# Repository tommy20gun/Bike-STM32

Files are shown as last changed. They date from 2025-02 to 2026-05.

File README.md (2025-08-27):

# E-Bike Infotainment System

## Software Module Summary
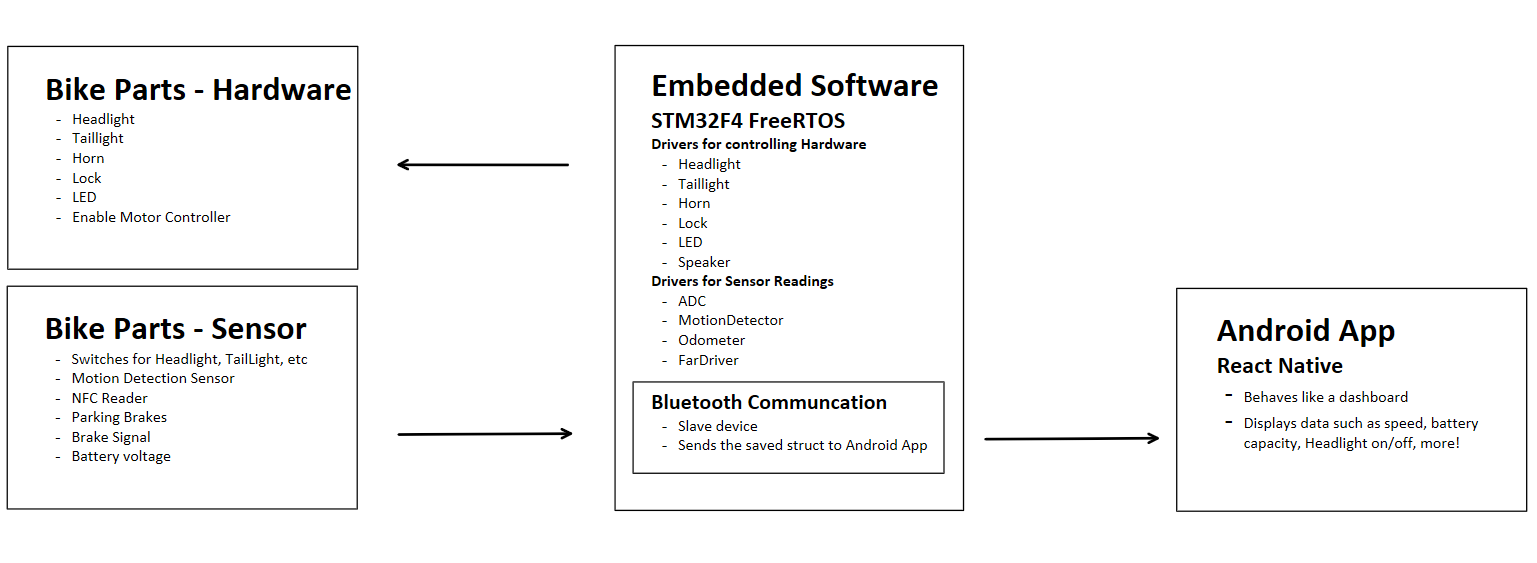
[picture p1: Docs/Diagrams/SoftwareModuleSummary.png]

The three modules are comprised of **Hardware, Embedded Software, and Android App Software.**
- The Microcontroller is an STM32F4 microcontroller running **FreeRTOS**. Each peripheral has a separate task that handles the firmware drivers for its operation. This allows certain peripherals that demand **ontime scheduling** to get their share of clock cycles.
- Embedded Software contains drivers for accessing:
  - **headlights, tail lights, car horn** - GPIO debounced switch, mosfet, relays
  - **NFC scanner and keycard unlock** - SPI communication with NFC chip (PN532)
  - **PWM LED lights** - PWM driver for WS2812B to control color
  - **Human detection alarm** - Interrupt driven by IR sensor
  - **Serial communication** - UART DMA to Bluetooth module
  - **Battery monitoring** - ADC, battery curve implemented as a polynomial regression
  - **Speedometer** - Hall effect sensor on wheel
- The Microcontroller sends **Bluetooth (BLE) data** to the Android Tablet.
- The display is an Android Tablet running a **mobile app** created using **React Native**

<a href="https://github.com/tommy20gun/Bike-STM32/tree/master/CustomDrivers"><strong>Explore the Code » </strong> </a>

<p align="right">(<a href="#readme-top">back to top</a>)</p>

## Demo

### Turn Signals
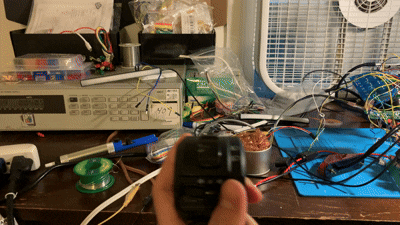
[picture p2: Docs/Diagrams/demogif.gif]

<p align="right">(<a href="#readme-top">back to top</a>)</p>

### Microcontroller Pinout -  KiCAD EDA:

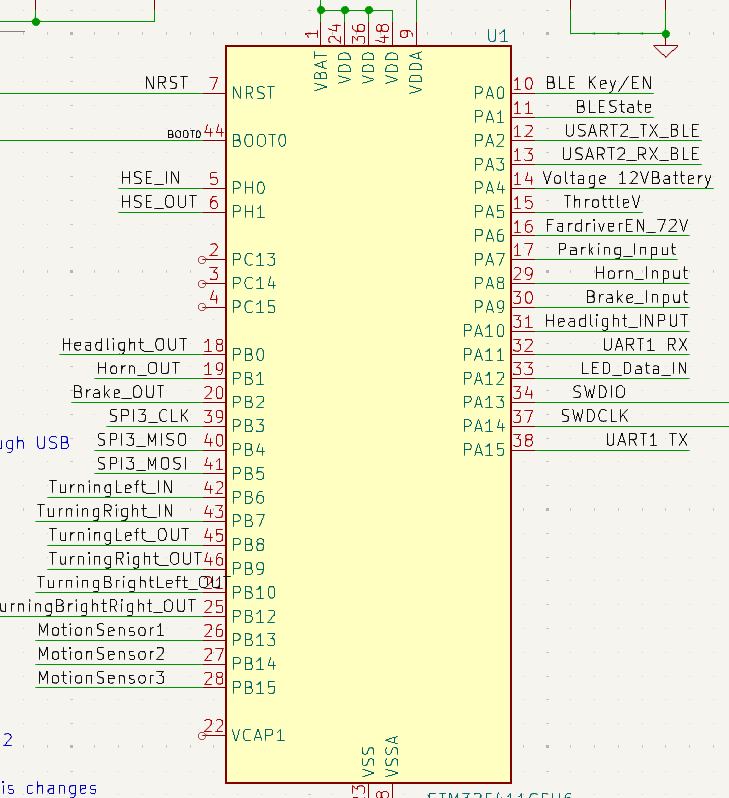
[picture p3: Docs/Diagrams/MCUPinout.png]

<a href="https://github.com/tommy20gun/Bike-STM32/tree/master/Docs/Diagrams/Bike_PCB.pdf"><strong>Explore the eCAD » </strong> </a>
<p align="right">(<a href="#readme-top">back to top</a>)</p>

### Battery Curve
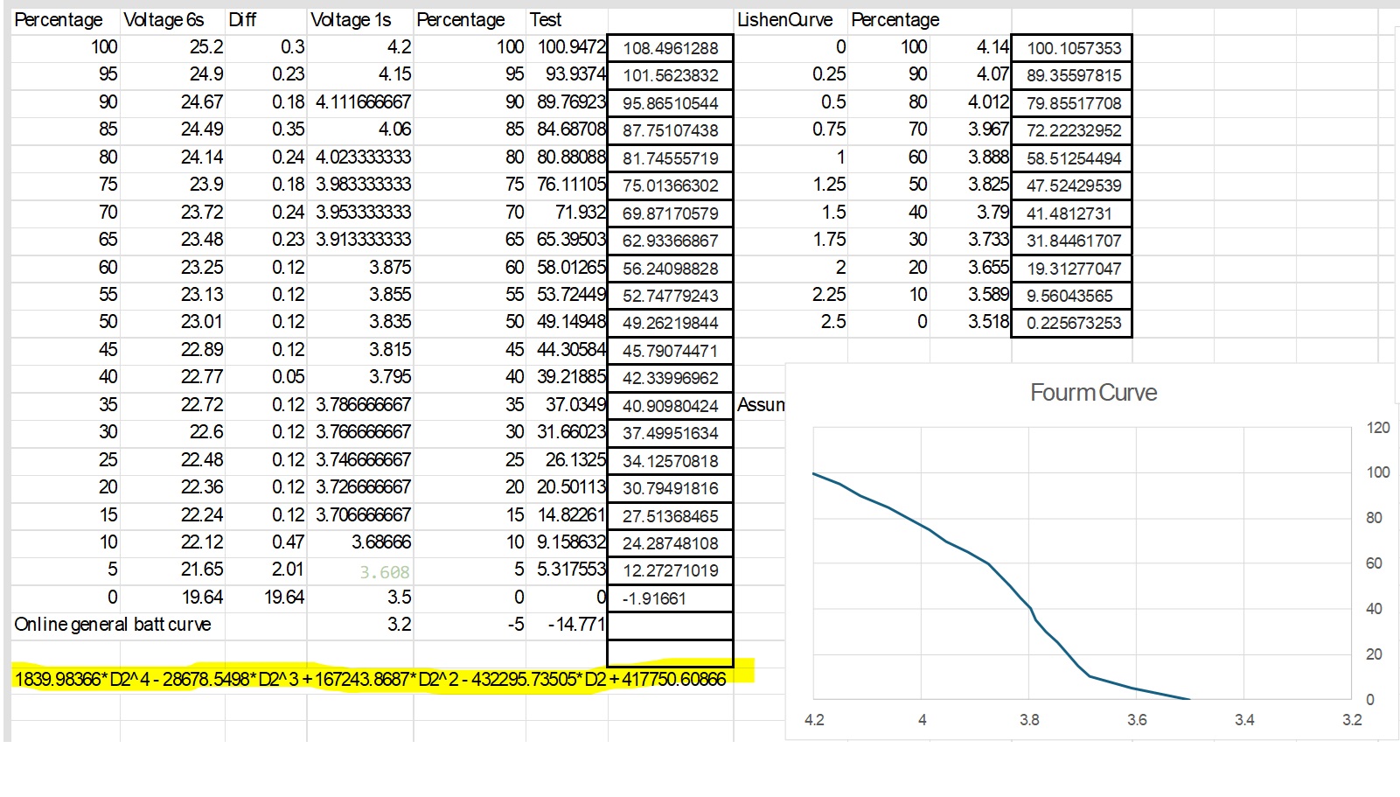
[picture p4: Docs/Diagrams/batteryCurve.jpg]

<p align="right">(<a href="#readme-top">back to top</a>)</p>

### State Machine Implementation of Lock

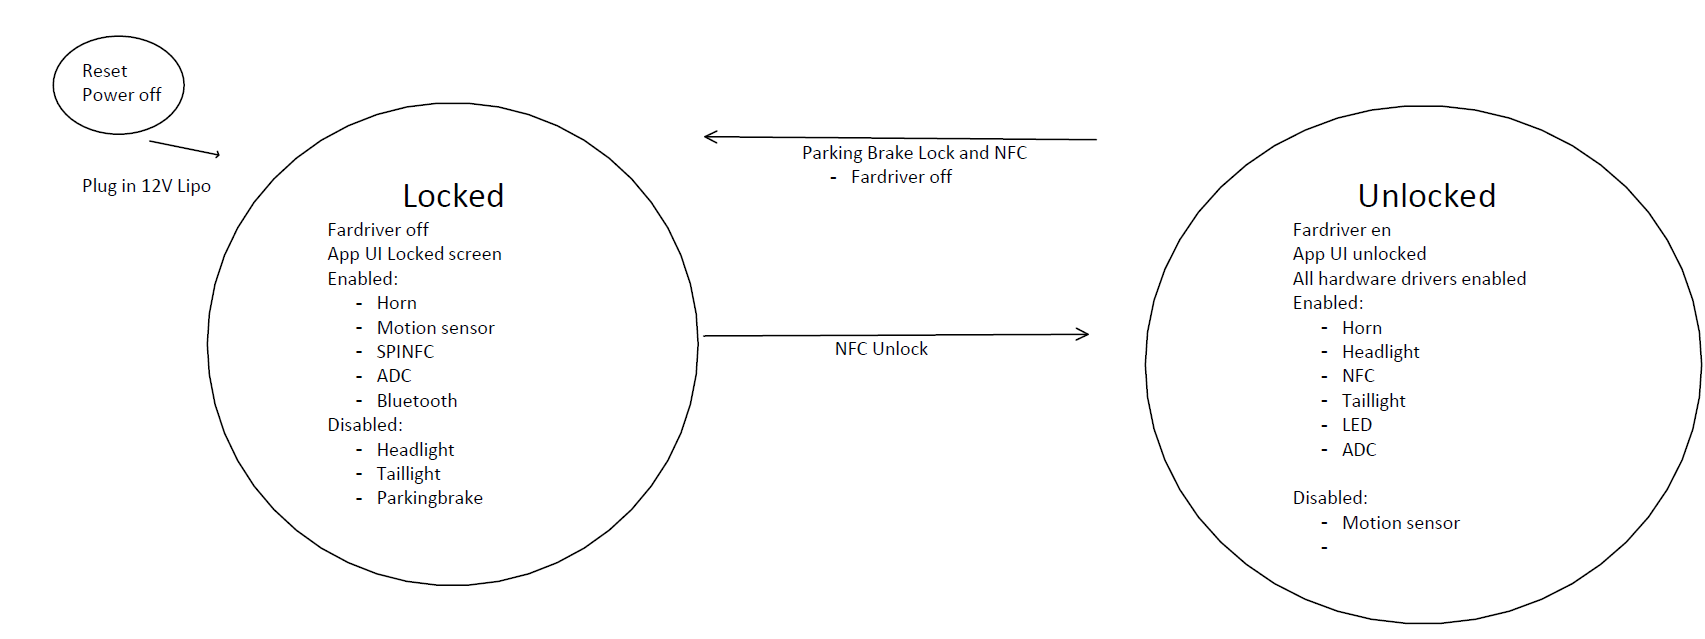
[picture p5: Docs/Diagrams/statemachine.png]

<p align="right">(<a href="#readme-top">back to top</a>)</p>

### Bike
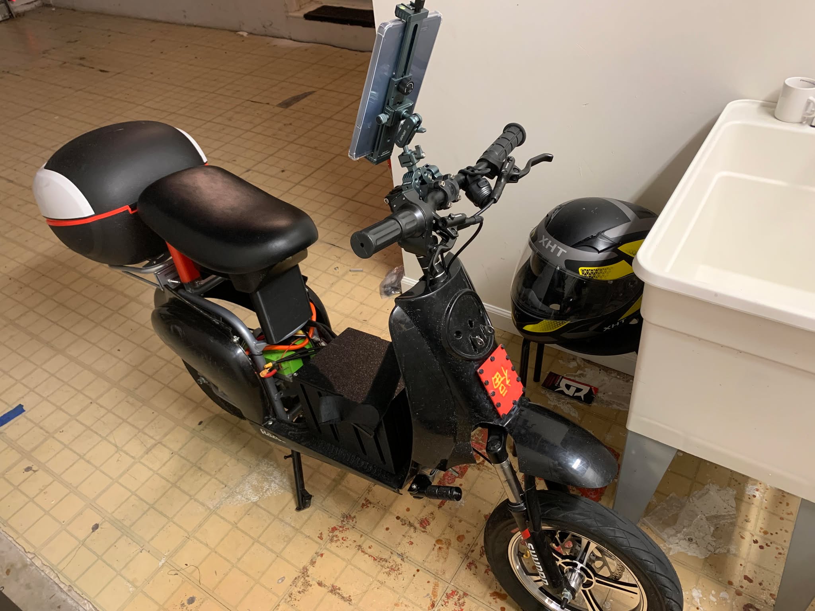
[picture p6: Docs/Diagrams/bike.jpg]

<!-- LICENSE -->
## License

Distributed under the MIT License. See `LICENSE-MIT.txt` for more information.

<p align="right">(<a href="#readme-top">back to top</a>)</p>

<!-- CONTACT -->
## Contact

Tommy Xu: xuhaohui20@gmail.com

<p align="right">(<a href="#readme-top">back to top</a>)</p>

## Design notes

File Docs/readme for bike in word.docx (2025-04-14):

# Smart E-Bike Project

This repository contains the implementation of a Tesla Center Console-like system mounted on an electric motorcycle.

- The display is an Android Tablet running a mobile app created using React Native
- Hardware I am controlling includes headlights, tail lights, car horn, NFC scanner and keycard unlock, cool LED lights, human detection alarm, and more!
- The Central Computer is an STM32F4 microcontroller running FreeRTOS. It allows all hardware to be controlled via the control cluster of the handlebar of the bike.
- The Central Computer sends Bluetooth data to the Android Tablet.

Below is a picture of the bike:

Below is a detailed diagram of each component and its features and functions:

Below is the state machine implementation of the Locking and Unlocking of the bike:

Below is the Microcontroller Pinout made with KiCAD EDA:

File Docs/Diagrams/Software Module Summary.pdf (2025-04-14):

# Headlight.h

- Setup GPIO EXTI,GPIO OD
- Toggle output on EXTI
•

# TailLight.h

Setup GPIO EXTI,GPIO OD,
Timer, GPIO PP

•

EXTI triggered inputs:
- Brake
- Left blink
- Right blink

•

- Blinks respective light at 1hz GPIO PP Hardware signal to FarDriver

•

Triggers a bluetooth command to blink on UI.

•

TODO: Should I poll the
variable and just call it a day?

•

# Drivers for controlling Hardware

Class Constructor runs the setup and creates RTOS task. Instance of object lives in mai

# Horn.h

- Setup GPIO EXTI,GPIO OD
- Toggle output on EXTI
•

# LED.h

- Setup DMA, GPIO PWM
Lights should move down its strand relative to the speed of the bike

•

Translate speed/ throttle
voltage of bike to speed of LED motion

•

Send data to light IC through DMA and PWN

•

## LEDMessage.h

Prepare the 32bit
message

•

Abstract color and
brightness

•

# Lock.h

- Setup SPI, GPIO PP, State Locked
- SPI CS En
- NFC Hardcoded Password
- SPI read toggles lock state Parking_Input pin moves state Unlocked -> locked. Does not unlock the bike

•

- Parking_Input disables Fardriver Sends BLE commands for locked and unlocked state

•

Triggers alarm upon use of buttons in locked state

•

TODO later: implement low
power mode into this

# MotionDetector

- Setup GPIO Input
- Activate on Lock state
- Deactivate on Unlock state Implement detection threshold algorithm

•

Enable Speaker/Horn on
detection

•

# Speaker.h

# ADC.h

12V battery. 3:1 voltage divider with outside resistor going into analog pin.

•

- Throttle V

# Bluetooth.h - BLE Slave device

### BluetoothSendslow()

Bluetooth TX Pollling 5hz using DMA since the data struct will be stationary

BluetoothSendFast()
Bluetooth TX Polling 50hzusing DMA since the data struct will be stationary

### BluetoothSendSpecialCom mand()

Upon request notify the
master(phone) of a change in state

BMSMOSon() should be a
command sent to ANTBMS

# React Native App - Android

Display
- Speedometer
- Odometer
- Wattage/Current
- RPM/ThrottleV
- Battery percentage: 12V, 72V optional
- TurnSIgnal Blink
- MotorTemp
- HeadlightON
- Brake On
- HornON is a red screen LOL
- Bool* BMSMOSOn (optional) sent to antBMS as a command 'A5A5FA0000FA' # Turn Off Charge MOSFET 'A5A5FA0001FB' # Turn On Charge MOSFET 'A5A5FE0000FE' # Reboot BMS
'A5A5F90000F9' # Turn Off DisCharge MOSFET 'A5A5F90001FA' # Turn On DisCharge MOSFET
'A5A5FC0000FC' # Toggles balancing

From <https://diysolarforum.com/threads/for-those-of-you-looking-to-monitor-your-ant-bms-with-pi3-via-bluetooth.6726/page-5> (https://diysolarforum.com/threads/for-those-of-you-looking-to-monitor-your-ant-bms-with-pi3-via-bluetooth.6726/page-5)

# Fardriver

# ANT BMS BT2.0

## Data sent

ANT BMS
This is bluetooth 2.0
0xDBDB00000000 to Receive 140 bytes of data
Python code: For those of you looking to monitor your ANT-BMS with
Pi3 via Bluetooth. | Page 4 | DIY Solar Power Forum (https://diysolarforum.com/threads/for-those-of-you-looking-to-monitor-your-ant-bms-with-pi3-via-bluetooth.6726/page-4)
- Current
- Pack Voltage
- unitVDiff
- All Cell Unit V (optional)
- Battery Temperature (optional)

# - 12V Lipo - Throttle potentiometer

# Buttons and Sensors

- HeadlightON/ HeadlightOFF
- Turn Signal Left/Right/OFF
- HornON
- ParkingON
- Boost (optional)
- 3 motion detection sensor
- NFC Reader

# Hardware

# Embedded Software - STM32F4

- Headlights
- Tailight
- Horn
- LED
- Speakers
- Brake
- FardriverEnable 72V

# Bike Parts - Output

# Bike Parts - Input

Commands to send to Controller (once low power mode is enabled)
- Turn on Horn
- Turn on Light
- Turn on LED

# Odometer.h

- EEPROM emulation on variable Calculates Odometer reading based on dspeed/dtime

•

Optional
- Set up GPIO Exti
- Trigger every Hall Effect contact Update odometer per increment of wheel rotation

•

### Setup using AT Commands

- Configured as slave
Pair bind link to the phone to allow for connection in range (done on master device)

- Name:deez nuts
- PW: 6969
- Baud:9600
- Stop:1
- Parity 0

TODO: switch on circuit board to allow for programming in AT mode

TODO Turn the EN pin to input to read the switch whether want AT mode or regular

- Uint32_t magic number = 69420
- Bool* HeadlightON
- Double* MotorTemp
- Double* ADCreading72V
- Double* ADCreading12V
- Double* Battery temp
- Struct* PackVoltage(optional)
- Double* Odometer (Persistent)

# Bluetoth Communication HashTable

- Currently lives in bluetooth.h
- There won't be race conditions using a freeRTOS queue. 1 source of writing This will change when Android commands are introduced, the UART channel needs mutex before

- Error check with CRC
Use a Queue to send data to the packing struct, once the queue is empty then data can be sent.

- Priority for sending is lower than hardware buttons
- Double* speed
- Bool* HornON
- Bool* BrakeON
- Bool* TurningLeft
- Bool* TurningRight
- Int* RPM
- Double* Current
- Double* throttleV
- State_t* locked
- State_t* unlocked
- uint32_t CRC

# FarDriver.h

- RPM
- Motor Temperature

Wiring method

GPIO input with timer on 5v tolerant pins

•

ADC read the temperature
sensor

•

Bluetooth method
Baud:19200. data format is noted here. Just try to receive it using HC-05 serial
fardriver-controllers/README.md at main · jackhumbert/fardriver-controllers (https://github.com/jackhumbert/fardriver-controllers/blob/main/README.md)

# Drivers for sensor readings

Attempt with BLE bc there is a chance ANT BMS is BLE

# Watchdog timer

# Software Module Summary

Tuesday, February 4, 2025 9:51 PM

New Section 2 Page 1

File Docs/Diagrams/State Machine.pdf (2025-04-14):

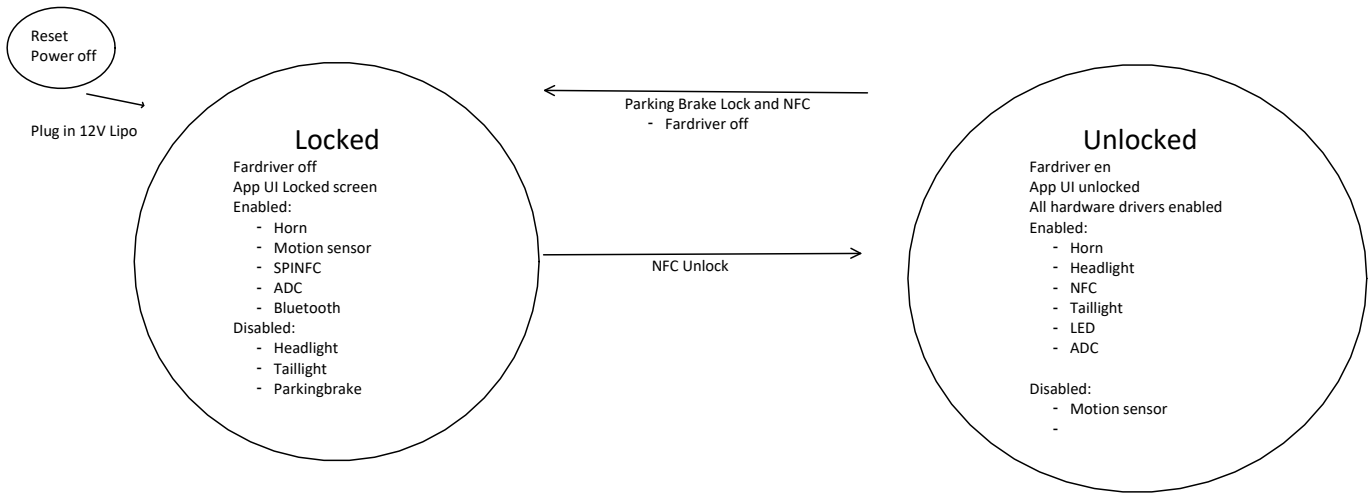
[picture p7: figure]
NFC Unlock; Parking Brake Lock and NFC - Fardriver off Locked; Fardriver off App UI Locked screen Enabled: - Horn - Motion sensor - SPINFC - ADC - Bluetooth Disabled: - Headlight - Taillight - Parkingbrake; Unlocked; Fardriver en App UI unlocked All hardware drivers enabled Enabled: - Horn - Headlight - NFC - Taillight - LED - ADC; Disabled: - Motion sensor -; Reset Power off; Plug in 12V Lipo

Main ()
RTOS task state machine:
- state transition lock to unlock
- State transition unlocked to lock

vtasksuspend() and vtaskresume() is implemented depending on the transition Or use a class specific state transition function

Lock.cpp (only the drivers to send an event)
Read lock and send the event to the state transition task

# State Machine

Wednesday, February 5, 2025 4:59 PM

New Section 2 Page 1

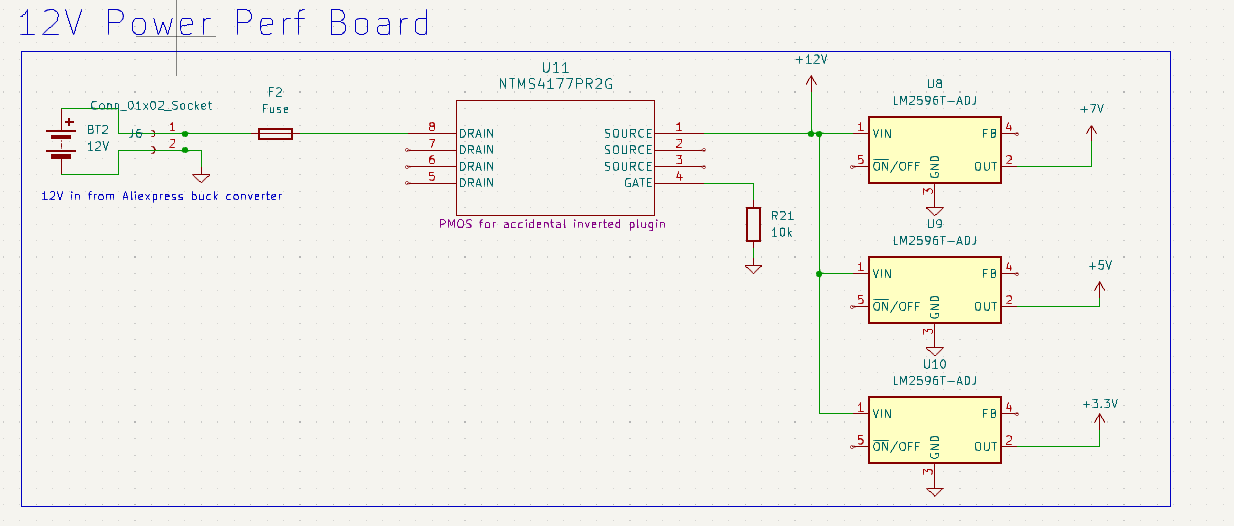
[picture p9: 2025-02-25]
Docs/Diagrams/KiCAD Power.png

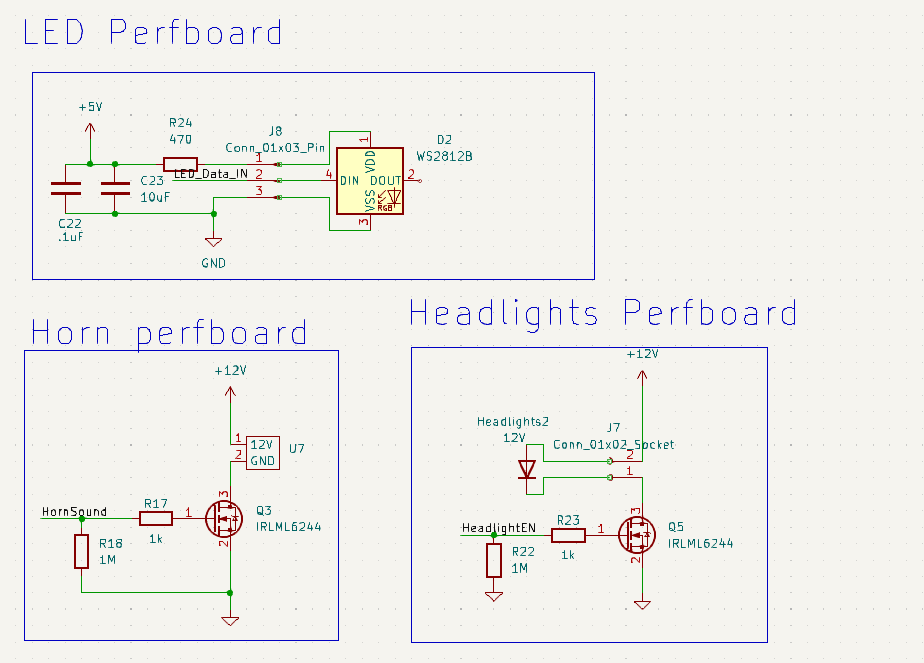
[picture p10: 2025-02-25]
Docs/Diagrams/KiCAD etc.png

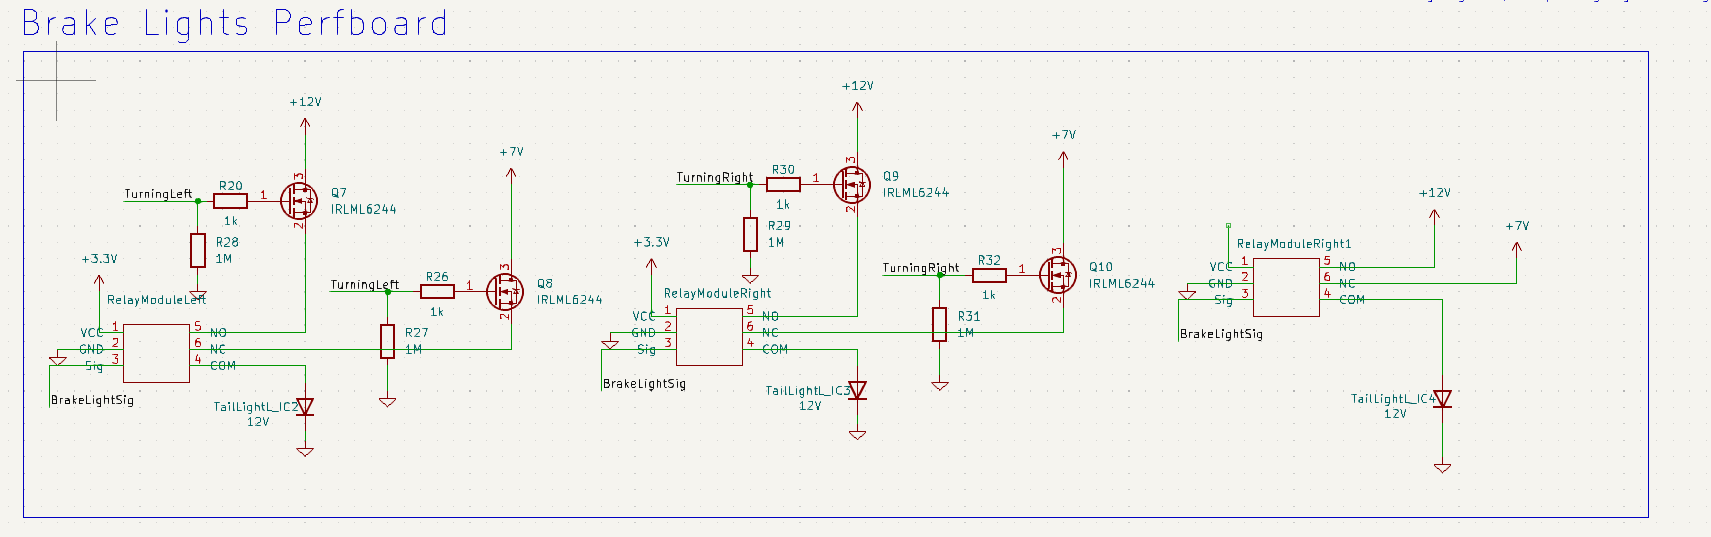
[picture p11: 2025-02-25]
Docs/Diagrams/KiCAD brake lights.png

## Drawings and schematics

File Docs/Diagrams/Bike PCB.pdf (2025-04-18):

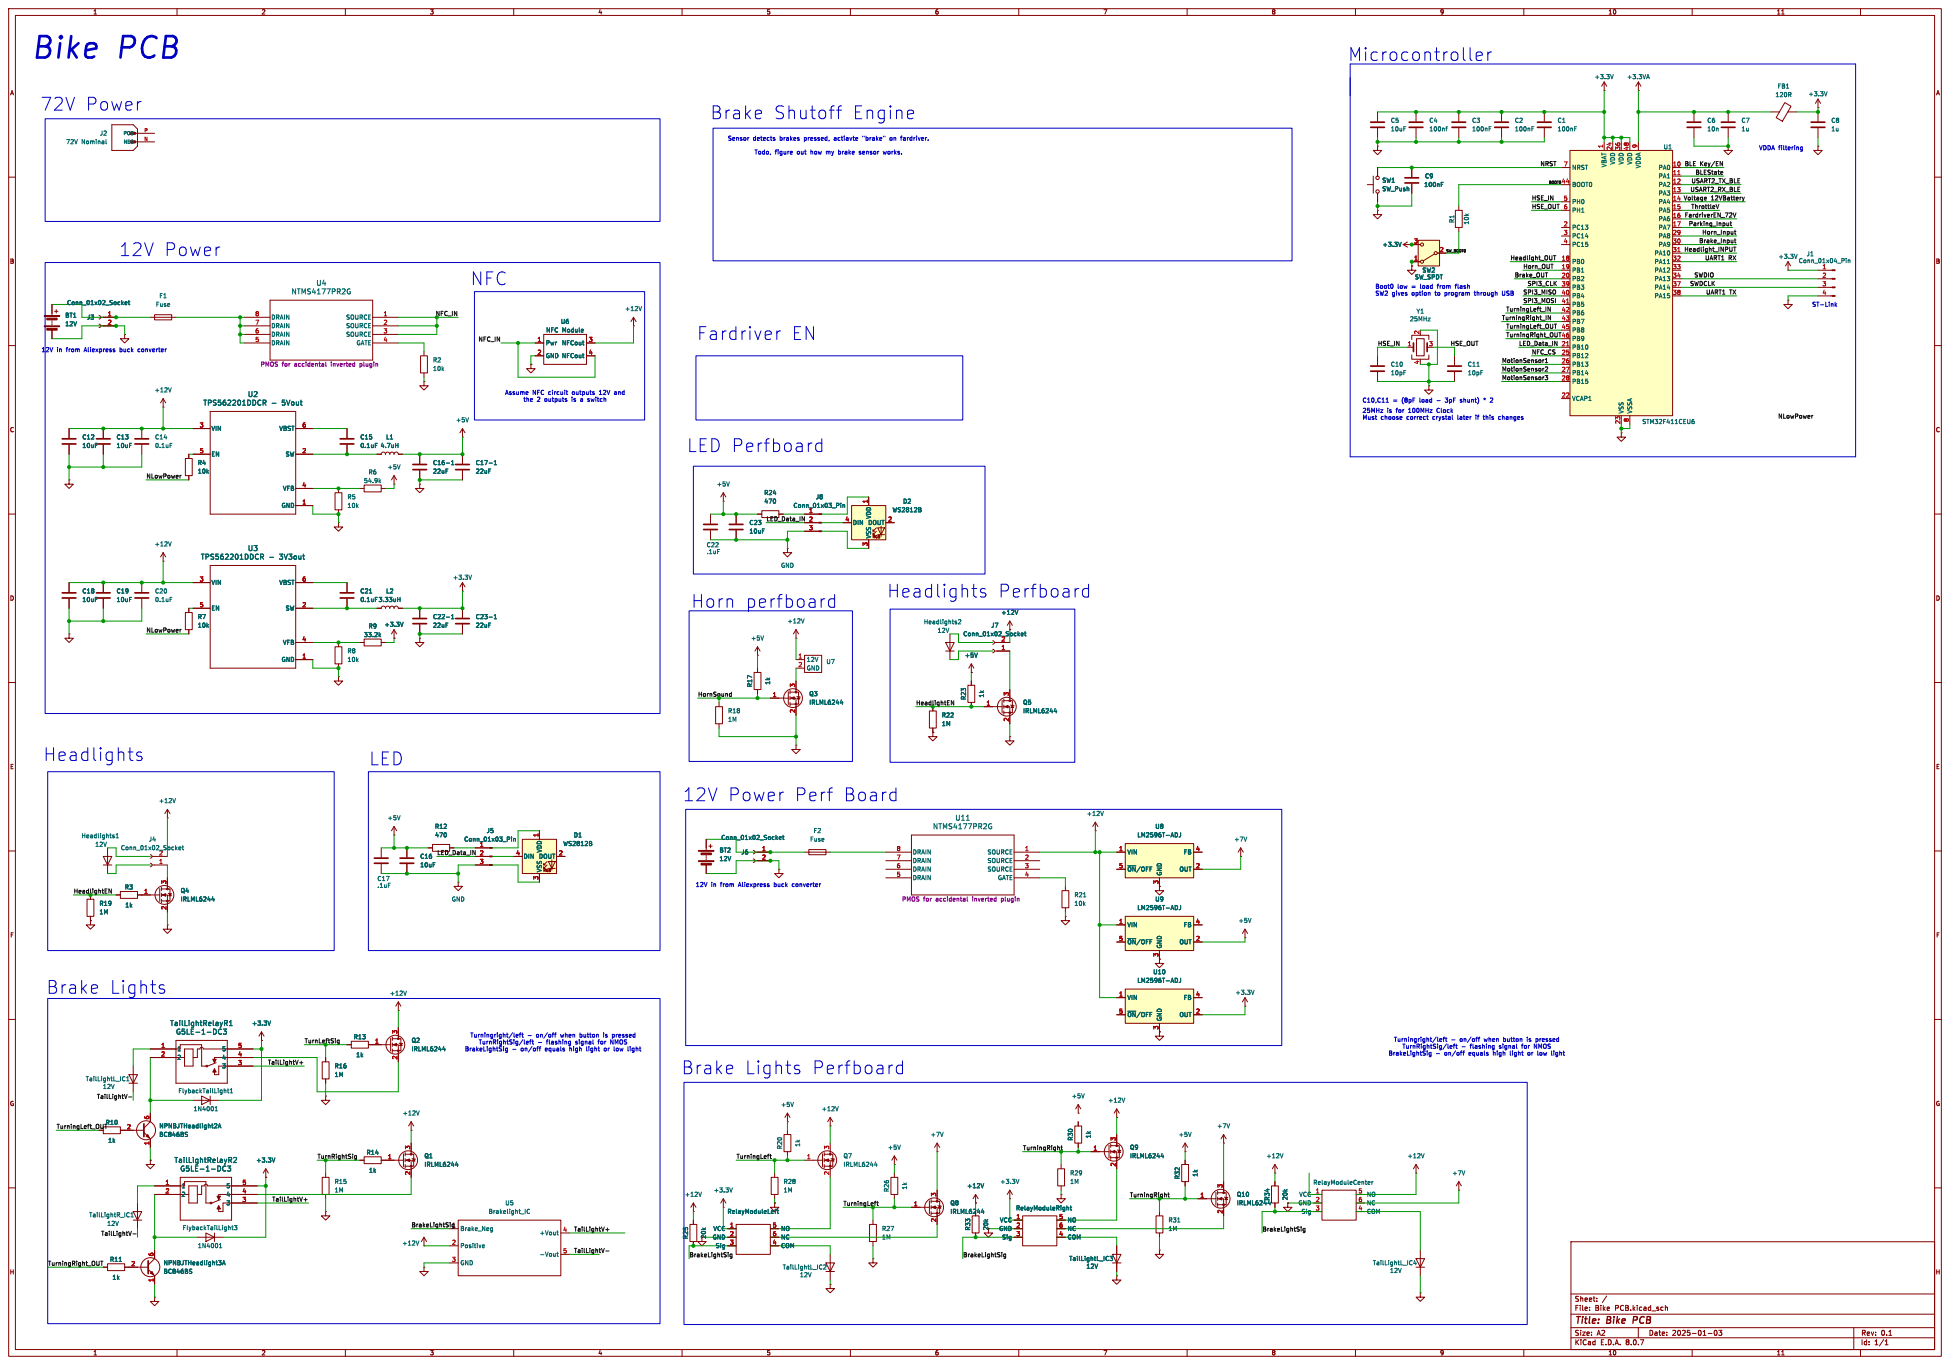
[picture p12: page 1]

ST-Link C10,C11 = (8pF load - 3pF shunt) * 2

25MHz is for 100MHz Clock Must choose correct crystal later if this changes (https://www.digikey.com/en/products/detail/ecs-inc/ECS-250-9-37B2-CKM-TR/14663267)

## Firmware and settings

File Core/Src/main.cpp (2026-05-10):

 /** 
  * 
  * @brief          : Main program body
  * 
  * This is the main body of the program. The MCU will run setup code such as Clock config, ISRVector table, and start the RTOS.
  * Implements state machine.
  *
  * 
  */

#include "main.h" //includes LL
#include <string>

#include "Peripheral_initialization.h"

//CPP includes
#include "Headlight.h"
#include "Horn.h"
#include "Bluetooth.h"
#include "MemoryMap.h"
#include "Speedometer.h"
#include "Motion_Detector.h"
#include "LED.h"
#include "Lock.h"
#include "Taillight.h"
#include "ADC.h"
#include "SwitchActivatedDevice.h"


static Horn* horn;
static ShortHorn* shorthorn;
static Headlight* headlight;
static TailLight_Turn* left;
static TailLight_Turn* right;
static TailLight_Brake* brake;
static Bluetooth* bluetooth;
static ADCDriver* adc;
static Lock* bikelock;
static Motion_Detector* detector1;
static Speedometer* speedometer;
//static Motion_Detector* detector2;
//static Motion_Detector* detector3;

static TaskHandle_t stateMachineHandle;
static state_t state;
static QueueHandle_t messenger;

/* create tasks, create object instances. object constructors set up hardware and own the semaphore*/
void GlobalSetup(void){
    //create global queue, assign to all obj
  messenger = xQueueCreate(30,sizeof(struct uint32_t_Buffer));
  BaseType_t xReturned = xTaskCreate(state_machine, "state_machine", 64, NULL, 2, &stateMachineHandle);
  if (xReturned != pdPASS){
    Error_Handler();
  }

  horn = new Horn(GPIOA,GPIO_PIN_8,GPIOB,GPIO_PIN_1,messenger,HORN_ON);
  shorthorn = new ShortHorn(GPIOB,GPIO_PIN_14, GPIOB,GPIO_PIN_1,messenger,HORN_ON);
  headlight = new Headlight(GPIOA,GPIO_PIN_10,GPIOB,GPIO_PIN_0,messenger,HEADLIGHT_ON);
  left = new TailLight_Turn(GPIOB,GPIO_PIN_6,GPIOB,GPIO_PIN_8,GPIOB,GPIO_PIN_10,messenger,TURNING_LEFT);
  right = new TailLight_Turn(GPIOB,GPIO_PIN_7,GPIOB,GPIO_PIN_9,GPIOB, GPIO_PIN_12,messenger,TURNING_RIGHT);
  brake = new TailLight_Brake(GPIOA,GPIO_PIN_9,GPIOA,GPIO_PIN_5,messenger,BRAKE_ON);
  bluetooth = new Bluetooth(messenger); //bluetooth hard coded to PA2,PA3
  adc = new ADCDriver(messenger, GPIOA, GPIO_PIN_4, GPIO_PIN_0); //VOLTAGE_12V_BATT and PERCENT_12V_BATT are hardcoded. channel4 (12V) PA4 is hardcoded. So is Queuetag
  bikelock = new Lock(GPIOA,GPIO_PIN_7,GPIOA,GPIO_PIN_6,messenger,STATE_MACHINE_STATUS,stateMachineHandle);
  speedometer = new Speedometer(messenger, GPIOA, GPIO_PIN_1);
  //detector1 = new Motion_Detector(messenger,HEADLIGHT_ON, GPIOB, GPIO_PIN_13);
  xTaskNotify(stateMachineHandle, 2, eSetValueWithOverwrite); //increments notif value by 1. TODO this is wrong bc then state 1 is unlock but I should check notified value to confirm.
}

//TODO there is a possiblity to implement lock level 2 for motion detection
/*
State machine should stay in main
*/
void state_machine(void* pvParameters){
  state = STATE_START;
  typedef state_t (*state_Transition)(state_t);
  state_Transition transitiontable[3] = {lock,unlock, start};
  uint32_t notifiedValue = 0;
  while(1){
    xTaskNotifyWait(0, 2U, &notifiedValue, portMAX_DELAY); //Start is not block bc of this  xTaskNotify(stateMachineHandle, 2, eSetValueWithOverwrite); //increments notif value by 1. TODO this is wrong bc then state 1 is unlock but I should check notified value to confirm.

    //notified value is the same enumeration where 1 calls unlock 0 calls locked
    //STATE_UNLOCKED = 1
    //STATE_LOCKED = 0
    if (state == STATE_START){
      state = transitiontable[notifiedValue & 3U](state); //reads the last bit to determine 0 or 1
    }
    else {
      state = transitiontable[notifiedValue & 1U](state); //reads the last bit to determine 0 or 1
    }
  }
}
//TODO future make this an event group where the notification uint32 has mapping of each task handle
/*
FardriverEN_72V - PA6
*/
state_t unlock(state_t state){
  if (state == STATE_LOCKED){
    vTaskResume(horn->getTaskHandle());
    vTaskResume(left->getTaskHandle());
    vTaskResume(right->getTaskHandle());
    vTaskResume(brake->getTaskHandle());
    LL_GPIO_ResetOutputPin(GPIOA,GPIO_PIN_6); //fardriver Pin
    //vTaskResume(LED);
    //vTaskSuspend(detector1->getTaskHandle());
    honkHorn(state);
    //log stateUnlocked suscessful
    return STATE_UNLOCKED;
  }
  //log stateunlocked failed
  return STATE_LOCKED;
}
/*
FardriverEN_72V - PA6
*/
state_t lock(state_t state){
  if (state == STATE_UNLOCKED){
    vTaskSuspend(horn->getTaskHandle());
    vTaskSuspend(left->getTaskHandle());
    vTaskSuspend(right->getTaskHandle());
    vTaskSuspend(brake->getTaskHandle());
    LL_GPIO_SetOutputPin(GPIOA,GPIO_PIN_6); //fardriver Pin will close OD, close relay, locking the bike 
    //vTaskSuspend(LED);
    //vTaskResume(detector1->getTaskHandle());
    honkHorn(state);
    //log stateUnlocked suscessful
    return STATE_LOCKED;
  }
  //log stateunlocked failed
  return STATE_UNLOCKED;
}

state_t start(state_t state){
  if (state == STATE_START){
    LL_GPIO_SetOutputPin(GPIOA,GPIO_PIN_6); //fardriver Pin will close OD, close relay, locking the bike 
    vTaskSuspend(horn->getTaskHandle());
    vTaskSuspend(left->getTaskHandle());
    vTaskSuspend(right->getTaskHandle());
    vTaskSuspend(brake->getTaskHandle());
    //vTaskSuspend(LED);
    vTaskResume(detector1->getTaskHandle());
    //log stateUnlocked suscessful
    return STATE_LOCKED;
  }
  //log stateunlocked failed
  return state;
}

void honkHorn(state_t func_call_state){
  if (func_call_state == STATE_UNLOCKED || func_call_state == STATE_START){ //lock is 1 beep
    LL_GPIO_SetOutputPin(GPIOB, LL_GPIO_PIN_1);
    vTaskDelay(10);
    LL_GPIO_ResetOutputPin(GPIOB, LL_GPIO_PIN_1);
  }
  else {//unlock is 2 beep
    LL_GPIO_SetOutputPin(GPIOB, LL_GPIO_PIN_1);
    vTaskDelay(10);
    LL_GPIO_ResetOutputPin(GPIOB, LL_GPIO_PIN_1);
    vTaskDelay(100);
    LL_GPIO_SetOutputPin(GPIOB, LL_GPIO_PIN_1);
    vTaskDelay(10);
    LL_GPIO_ResetOutputPin(GPIOB, LL_GPIO_PIN_1);
  }
}

int main(){
  //HAL_Init(); //TODO Try to run code without this
  SystemClock_Config();
  GPIO_GlobalSetup();
  GlobalSetup();
  vTaskStartScheduler();
}

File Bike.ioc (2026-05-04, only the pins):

Mcu.UserName=STM32F411CEUx
PA1.Signal=ADCx_IN1
PA10.Signal=GPXTI10
PA11.Signal=GPXTI11
PA12.Signal=GPXTI12
PA13.Signal=SYS_JTMS-SWDIO
PA14.Signal=SYS_JTCK-SWCLK
PA2.Signal=USART2_TX
PA3.Signal=USART2_RX
PA4.Signal=ADCx_IN4
PA5.Signal=ADCx_IN5
PA7.Signal=GPXTI7
PB12.Signal=GPIO_Input
PB13.Signal=GPIO_Input
PB14.Signal=GPIO_Input
PB3.Signal=SPI3_SCK
PB4.Signal=SPI3_MISO
PB5.Signal=SPI3_MOSI
PB8.Signal=GPIO_Output
PB9.Signal=GPIO_Output
PC13-ANTI_TAMP.Signal=GPIO_Output

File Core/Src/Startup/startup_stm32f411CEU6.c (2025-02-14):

 /** 
  * 
  * @brief          : Set up vector table and reset entry point
  * 
  * Performs Reset Handler by allocating memory addresses and running main.
  * Creates ISRVector table.
  * 
  * Translation of startup_stm32f411xe.s which is in ARM Assembly. 
  * 
  */

#include <stdint.h>
#include <system_stm32f4xx.h>
#include <stm32f4xx.h>

/* address from Linker */
/*flash*/
extern uint32_t  _sidata; //start of data in flash
/* ram */
extern uint32_t _sdata; //start of data in ram
extern uint32_t _edata; //end of data in ram
extern uint32_t _sbss; //start of data in bss
extern uint32_t _ebss; //end of data in bss
extern uint32_t _estack; //stack pointer

//find all c++ objects and "execute" constructors
extern void __libc_init_array();
extern int main();

//main entry point to the program
void Reset_Handler(void){
	
    uint32_t* sidata = &_sidata;
    uint32_t* sdata = &_sdata;
    uint32_t* edata = &_edata;
    //move from flash into static ram
    while(sdata < edata){
        *sdata = *sidata;
		sdata++;
		sidata++;
    } 
    
	uint32_t* sbss = &_sbss;
	uint32_t* ebss = &_ebss;
    //initialize bss as 0
	while(sbss < ebss){
		*sbss = 0;
		sbss++;
	}
	
    SystemInit();
	//find all c++ objects and "execute" constructors
    __libc_init_array();
    main();

    /* code needs to execute if main somehow returns by accident*/
    while(1);

}
//unimplemented interrupts
void DefaultHandler(void){
	while(1);
}



//initialize all interrupt functions but give them the weak attribute so that it will use defaultHandler unless the function is implemented
__weak void   NMI_Handler(void){ DefaultHandler();}
__weak void   HardFault_Handler(void){DefaultHandler();}
__weak void   MemManage_Handler(void){ DefaultHandler();}
__weak void   BusFault_Handler(void){ DefaultHandler();}
__weak void   UsageFault_Handler(void){ DefaultHandler();}
__weak void   SVC_Handler(void){ DefaultHandler();}
__weak void   DebugMon_Handler(void){ DefaultHandler();}
__weak void   PendSV_Handler(void){ DefaultHandler();}
__weak void   SysTick_Handler(void){ DefaultHandler();}

/* External Interrupts */
__weak void      WWDG_IRQHandler                   (void){ DefaultHandler();}/* Window WatchDog              */                                        
__weak void      PVD_IRQHandler                    (void){ DefaultHandler();}/* PVD through EXTI Line detection */                        
__weak void      TAMP_STAMP_IRQHandler             (void){ DefaultHandler();}/* Tamper and TimeStamps through the EXTI line */            
__weak void      RTC_WKUP_IRQHandler               (void){ DefaultHandler();}/* RTC Wakeup through the EXTI line */                      
__weak void      FLASH_IRQHandler                  (void){ DefaultHandler();}/* FLASH                        */                                          
__weak void      RCC_IRQHandler                    (void){ DefaultHandler();}/* RCC                          */                                            
__weak void      EXTI0_IRQHandler                  (void){ DefaultHandler();}/* EXTI Line0                   */                        
__weak void      EXTI1_IRQHandler                  (void){ DefaultHandler();}/* EXTI Line1                   */                          
__weak void      EXTI2_IRQHandler                  (void){ DefaultHandler();}/* EXTI Line2                   */                          
__weak void      EXTI3_IRQHandler                  (void){ DefaultHandler();}/* EXTI Line3                   */                          
__weak void      EXTI4_IRQHandler                  (void){ DefaultHandler();}/* EXTI Line4                   */                          
__weak void      DMA1_Stream0_IRQHandler           (void){ DefaultHandler();}/* DMA1 Stream 0                */                  
__weak void      DMA1_Stream1_IRQHandler           (void){ DefaultHandler();}/* DMA1 Stream 1                */                   
__weak void      DMA1_Stream2_IRQHandler           (void){ DefaultHandler();}/* DMA1 Stream 2                */                   
__weak void      DMA1_Stream3_IRQHandler           (void){ DefaultHandler();}/* DMA1 Stream 3                */                   
__weak void      DMA1_Stream4_IRQHandler           (void){ DefaultHandler();}/* DMA1 Stream 4                */                   
__weak void      DMA1_Stream5_IRQHandler           (void){ DefaultHandler();}/* DMA1 Stream 5                */                   
__weak void      DMA1_Stream6_IRQHandler           (void){ DefaultHandler();}/* DMA1 Stream 6                */                   
__weak void      ADC_IRQHandler                    (void){ DefaultHandler();}/* ADC1, ADC2 and ADC3s         */                                 
__weak void      EXTI9_5_IRQHandler                (void){ DefaultHandler();}/* External Line[9:5]s          */                          
__weak void      TIM1_BRK_TIM9_IRQHandler          (void){ DefaultHandler();}/* TIM1 Break and TIM9          */         
__weak void      TIM1_UP_TIM10_IRQHandler          (void){ DefaultHandler();}/* TIM1 Update and TIM10        */         
__weak void      TIM1_TRG_COM_TIM11_IRQHandler     (void){ DefaultHandler();}/* TIM1 Trigger and Commutation and TIM11 */
__weak void      TIM1_CC_IRQHandler                (void){ DefaultHandler();}/* TIM1 Capture Compare         */                          
__weak void      TIM2_IRQHandler                   (void){ DefaultHandler();}/* TIM2                         */                   
__weak void      TIM3_IRQHandler                   (void){ DefaultHandler();}/* TIM3                         */                   
__weak void      TIM4_IRQHandler                   (void){ DefaultHandler();}/* TIM4                         */                   
__weak void      I2C1_EV_IRQHandler                (void){ DefaultHandler();}/* I2C1 Event                   */                          
__weak void      I2C1_ER_IRQHandler                (void){ DefaultHandler();}/* I2C1 Error                   */                          
__weak void      I2C2_EV_IRQHandler                (void){ DefaultHandler();}/* I2C2 Event                   */                          
__weak void      I2C2_ER_IRQHandler                (void){ DefaultHandler();}/* I2C2 Error                   */                            
__weak void      SPI1_IRQHandler                   (void){ DefaultHandler();}/* SPI1                         */                   
__weak void      SPI2_IRQHandler                   (void){ DefaultHandler();}/* SPI2                         */                   
__weak void      USART1_IRQHandler                 (void){ DefaultHandler();}/* USART1                       */                   
__weak void      USART2_IRQHandler                 (void){ DefaultHandler();}/* USART2                       */                   
__weak void      EXTI15_10_IRQHandler              (void){ DefaultHandler();}/* External Line[15:10]s        */
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

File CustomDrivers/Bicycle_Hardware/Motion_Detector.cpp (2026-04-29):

 /** 
  * 
  * @brief          : Driver to control Motion Detector
  * 
  * Driver to control Motion Detector circuit. 
  * Implementation of the detection threshold algorithm
  * 
  * GPIO EXTI 1- PB13
  * GPIO EXTI 2- PB14
  * GPIO EXTI 3- PB15
  * 
  * account for standby phase of 1 minute on startup
  * Pin going low is "detected motion"
  * there is a delay of 3 seconds (blocked after the pin going back HIGH)
  * THere is an adjustable time delay during the last time motion is detected BEFORE pin going high again. 
  * 
  * Settings on breakoutboard:
  * Repeat Trigger
  * 3 second delay
  * 3 meters
  * 
  * Logic:
  * motion is detected for 5 seconds continuously: turn on all lights
  * motion is continually detected ~30 seconds honk the horn for 2 clicks every5 seconds
  * until motion is gone
  * 
  * on the activation or resume of a task, wait 60 seconds to initialize.
  * make sure the detector is able to signal when initialization is complete
  *
  */
#include "Motion_Detector.h"
void Motion_Detector::initTasks(){
    BaseType_t xReturned;
    xReturned = xTaskCreate(vTaskFunction,"Motion Detector",64, this,2,&TaskHandle);
    if(xReturned != pdPASS){
        Error_Handler();
    }
}

void Motion_Detector::initPeripherals(){
  LL_GPIO_InitTypeDef GPIO_InitStruct = {0};

  GPIO_InitStruct.Pin = readingPin.PinMask;
  GPIO_InitStruct.Mode = LL_GPIO_MODE_INPUT;
  GPIO_InitStruct.Pull = LL_GPIO_PULL_DOWN;
  LL_GPIO_Init(readingPin.GPIOx, &GPIO_InitStruct);

}
void Motion_Detector::QueueSend(){};//TODO I will impelemnt this later, it depends on how i want to send data

void Motion_Detector::vTaskFunction(void* pvParameters){
    Motion_Detector* detector = (Motion_Detector*) pvParameters;
    detector->RTOSImplementation();
}

void Motion_Detector::RTOSImplementation(){
    /*
    account for standby phase of 1 minute on startup
  * Pin going low is "detected motion"
  * there is a delay of 3 seconds (blocked after the pin going back HIGH)
  * THere is an adjustable time delay during the last time motion is detected BEFORE pin going high again. 
  * 
  * interrupt on falling edge, input pin polling until back to high, 
  * 
  * logic:
  * light is off
motion detector triggers
light turns on

There is motion
if light is off, then motion occurs, turn light on
if light is on from the switch, then motion occurs, nothing happens

There is no more motion
no more motion, headlight is on due to motion detector = turn off headlight
no more motion, headlight is on from light switch = turn off headlight
no more motion, headlight is off due to light switch = nothing
  * */
  //vTaskDelay(63000); // wait 1 minute for startup. The sensor should calibrate during this time so everytime
  // it becomes active (unlock->lock) state, it should do this calibration.
  struct uint32_t_Buffer buff;
  buff.tag = HEADLIGHT_ON;
  //bool previouspin = true;
  uint64_t timeON = 0;
  while(1){
    //executes when motion is detected
    if (LL_GPIO_IsInputPinSet(readingPin.GPIOx,readingPin.PinMask) == true){
      while (1){
        timeON +=30;
        if (timeON >= 500 && !LL_GPIO_IsOutputPinSet(GPIOA,GPIO_PIN_5)){
          LL_GPIO_ResetOutputPin(GPIOA,GPIO_PIN_5);
          buff.data = LL_GPIO_IsOutputPinSet(GPIOA,GPIO_PIN_5);
          xQueueSendToBack(messenger, &buff , 0);
          //previouspin = true;
        }
        //executes on falling edge only
        else if(LL_GPIO_IsInputPinSet(readingPin.GPIOx,readingPin.PinMask) == false /*&& previouspin == true*/){
          LL_GPIO_SetOutputPin(GPIOA,GPIO_PIN_5);
          buff.data = LL_GPIO_IsOutputPinSet(GPIOA,GPIO_PIN_5);
          xQueueSendToBack(messenger, &buff , 0);
          //previouspin = false;
          timeON = 0;
          vTaskDelay(3000); //lockout is 3sec
          break;
        }
        else{
          vTaskDelay(30);
        }
      }
    }
    vTaskDelay(100);
  } 
}

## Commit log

2025-02-08 Created new folders for Drivers, Clean up Makefile, main.h for LL
2025-02-08 Progress on RTOS with UART setup, Can compile w OsThreadDef and Main.cpp
2025-02-11 added Datasheet folder into Repo, fritzing
    [Light.fzz]
2025-02-12 Added DOCS folder with diagram and datsheetsubfolder, Created Bicycle Hardware files, Begin Documentation:file,brief,attention.
    [Light.fzz]
2025-02-20 fixed some compilation errors
    [Light.fzz]
2025-02-22 added headlight driver code copied from horn. Compiles but does not run
2025-02-23 interrupt does not work. Commit to generate cubemx code
    [main.cpp]
2025-02-23 EXTI function in main, compiles, does not work
    [main.cpp]
2025-02-23 Interrupt works!!
2025-02-23 fixed bug for starting high on taillight
    [TailLight.cpp]
2025-02-24 Begin code for UART setup with HC05
2025-02-25 Renamed files for Documentation
    [Light.fzz]
2025-02-26 generate code with LL UART DMA
2025-02-27 Finished Memory Mapping, finished DMA setup in Bluetooth.cpp (does not compile)
2025-02-27 remaining questions for DMA
2025-03-01 fixed some issues with compile
    [Bluetooth.cpp, main.cpp]
2025-03-03 progress to Bluetooth DMA
2025-03-03 DMA works
2025-03-05 generate CRC and ADC
2025-03-06 queue receive works. Need to debounce the switch
2025-03-12 ADC in progress
2025-03-12 ADC in progress 2
2025-03-12 commit battery charge curve and state machine planning
2025-03-13 compiled ADC
2025-03-14 updates on onenote and xlsx
    [Battery Discharge.xlsx]
2025-03-15 ADC works. Need to test with real circuit though
2025-03-16 generated SPI
2025-03-18 progress on SPI
2025-03-19 compiled Lock, did not implement PN532 drivers yet
2025-03-21 work on PN532 driver on onenote
2025-03-21 progress on lock driver
2025-04-02 more progress on lock driver
2025-04-07 Battery curve complete
2025-04-08 progress on SPI driver
2025-04-08 progress to spi transfer
2025-04-08 more progress on SPI Lock, did not implement parseReceivedCommand needed for testing.
2025-04-14 SPI still does not work
    [Lock.cpp, main.cpp]
2025-04-14 upload readme, restructure folders
    [Battery Discharge.xlsx, Light.fzz]
2025-04-17 pcb uploaded
    [Bike_PCB.kicad_sch]
2025-05-01 added transmitreceive function to see if it fixes it
    [Lock.cpp]
2025-05-05 Changed horn.cpp for testing debounce without interrupt
2025-05-24 debounced all buttons, horn.cpp tested
2025-06-04 Created "TESTING" preprocessor def for uart print debug, created ErrorHandler debug message, Cleared some TODOs,
    [Bluetooth.cpp, Lock.cpp, TailLight.cpp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]
2025-06-09 working bluetooth testing printout
2025-06-09 Tested working bluetooth printout
2025-06-11 Linker error fixed for virtual functions, ready for testing
    [main.cpp]
2025-06-18 Tested Headlight, Horn, Taillight towork. Now to do BLE, ADC
2025-06-20 compiled adc and bluetooth, untested.
2025-06-23 Working ADC and bluetooth, emptyqueue helper added
2025-07-22 give up on errorhandler error message. Printout still works
    [Light.fzz]
2025-07-26 tested motion detector code working
    [Light.fzz]
2025-07-27 finished Fritzing for connectors on MCU
    [Light.fzz]
2025-07-28 repin PB10,PB11
    [Light.fzz]
2025-07-28 compiled new Taillight Pin, untestested
2025-08-15 set all output pin to OD, added 5V pullup to fritzing
    [Light.fzz]
2025-08-15 changed taillight output pin to true for OD
2025-08-18 fix bug: blinker stays on at neutral turn signal Fritzing: to include 5vpullup and 5v relay board
    [Light.fzz]
2025-08-20 fixed state machine code to initialize on lock state
    [Light.fzz]
2025-08-27 repin PB2 to PA5, small change in readme and fritzing
    [Light.fzz]
2025-08-29 reduced lag for switch activated device
2025-08-29 change feature for tailight to remain on when default, switch the logic of relay OD pulldown
2025-08-29 suppress motion detector for testing, added mutex TODO for accessing certain pin resources for future
2025-09-05 got rid of Pin A5: ThrottleV, fixed hardcoded ADC setup
    [ADC.cpp, main.cpp]
2025-09-10 forgot to stage some files for previous commit
2025-09-12 Fritzing: wrote out fardriver throttle signal schematic
    [Light.fzz]
2025-09-12 fritzing:wrote out fardriver throttle signal schematic
    [Light.fzz]
2025-09-13 Added Brake activated throttle signal cut
2025-09-13 fixed inverted brake light bug
    [TailLight.cpp]
2025-10-11 disable horn on lock, enable brake light on lock, reverse brake light logic
    [TailLight.cpp, main.cpp]
2025-10-13 Shorten the horn honk. Test motion detection, disabled it. Set headlight to react to switch, taillight to on at startup
    [Horn.cpp, Motion_Detector.cpp, SwitchActivatedDevice.cpp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]
2025-10-24 saved onenote and todo for switchactivateddevice.cpp
2026-02-18 Reverse brakelight again: need to test
    [TailLight.cpp]
2026-02-18 add shorthorn obj, need to test
    [Horn.cpp, main.cpp]
2026-03-08 interrupt works
2026-03-08 shorthorn add delay and remove horn on pin reset
    [Horn.cpp]
2026-03-08 comment shorthorn for now
    [Light.fzz]
2026-03-09 fixed bug where brake unlocks bike in lock state
    [main.cpp]
2026-04-29 clean up adc raw
2026-04-30 fix speedometer virtual obj bug
    [Speedometer.cpp, main.cpp]
2026-04-30 CRC is settled on value of the brake
2026-05-01 adc to uint32 decimal 2 places, more queuesend for initialize pin state,
2026-05-02 adc works, lock is correct state, sample UI on input not output pin
    [ADC.cpp, Bluetooth.cpp, Lock.cpp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]
2026-05-02 disable uart rx so it doesn't trigger an interrupt that has not been set up yet
    [Bluetooth.cpp]
2026-05-04 update pins for future plans, including ADC on A1
    [Light.fzz]
2026-05-06 change voltage to display batt voltage not cell voltage
2026-05-07 UART done
2026-05-07 UART returns e0 when there is no connection, so just destroy that. Also in case data ==6, circular buffer prevents invalid mem access
    [Lock.cpp]
2026-05-10 lost track of progress, this build is on the bike, but headlight off doesn't work specifically on the bike
    [Light.fzz]
2026-05-10 throttle tune
2026-05-11 rpm is correct now, tune later if needed
    [Speedometer.cpp]
2026-05-22 okay working
    [Light.fzz]
